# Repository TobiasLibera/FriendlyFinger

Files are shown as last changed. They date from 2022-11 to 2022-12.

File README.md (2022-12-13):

# FriendlyFinger

A lovely stress relief device I designed while having a week off from work.<br></br>

## Description ##

The FriendlyFinger is a machine which rotates a 3D model of a middle finger from one side to the other, while having two LEDs shining a little lightshow to it.\
It's based on an ESP32 Development Board and is designed for remote control via WebServer or UDP.\
You need a 3D printer for building this project as well as you need to be willing to put some effort into it.
For example you will need to solder a little curcuit.<br></br>
I had a lot of fun developing and building the Friendly Finger.\
I do hope you gain something from building it, too.<br></br>

A Video can be found here:\
[Youtube Video](https://youtu.be/8vTFOdNh7Bw)<br></br>
Thingiverse:\
[Printing Data](https://www.thingiverse.com/thing:5678932)<br></br>

## Printing ##

### Before you start the Printing ###

<p><strong>
  There is a "FF_Template_Fits" part, which has all fits in it, that are needed for the assembly.
  The dimensions of the holes are the ones, that I use to get good fits.
  I strongly recommend to print this part at least once to check if all fits are working properly before printing the actual parts.
</strong><br>
</p>

The fits in the ```FF_Template_Fits``` part are:

<ol>
  <li>Fit with Nema17 Stepper motor
    <ol>
      <li>Nominal:    22mm</li>
      <li>My Value:   22.4mm</li>
    </ol>
  </li>
  <li>Fit to screw in a M3 screw directly into the printing part
    <ol>
      <li>Nominal:    3mm</li>
      <li>My Value:   2.93mm</li>
    </ol>
  </li>
  <li>Fit for RGB LED with an 28° angle to the vertical axis
    <ol>
      <li>Nominal:    5mm</li>
      <li>My Value:   5mm</li>
    </ol>
  </li>    
  <li>Countersunk hole for M3 screw (standard: ISO 4762)</li>
</ol>

Feel free to modify the corresponding STEP files to make this fits work properly.

### Cura Settings ###

<p><strong>
  Change the "Overhang Angle" in the Cura Support settings to 46 degrees.
</strong><br>
</p>

There is a BOM for the printing parts in the Documentations directory where you can find the Cura settings I used, how long the print took and how much filament was needed.
As mentioned, that are my settings. I am very sure there are a lot of folks out there who can find better, more effective settings for their prints.<br></br>

## Electronics ##

### Curcuit Board ###

<p><strong>
  I don't own any degrees in electronics!
  So I won't make any further advises on how to design the curcuit itself.
  All I do is giving an example without any warranty for safety and functionality.
</strong><br>
</p>

There is a wiring diagram in the "Documentation" directory, where the basics of the curcuit are shown in the way I planned them for my own work. It's missing headers for the RGB-LEDs as it's missing headers for the Step-Down voltage regulator.
  
  As I like JST headers and Dupoint headers, I used them for my own version.
Feel free to use whatever floats your boat to realize this connections.

### Nema 17 Stepper Motor ###

The Nema 17 I used to design this device for, has a body length of ***38mm***. As there are a lot of alternative dimensions for Nema 17 stepper motors, you can definitly use smaller ones for your device. It's not much force needed to rotate the middle finger model. I can't recommend to use bigger ones, as I didn't test it... if you get a bigger one working, let me know.

### Stepper Motor Driver ###

The ***DRV8825*** is the driver I designed the code and the curcuit for. You can, of course, choose the driver you want to, but maybe need to adjust the code and the curcuit.\
***BUT:***
As far as I had the Friendly Finger run in my living room, I realised that dissipated heat is sure an issue of my design. To solve the problem I adjusted the current to ***75% - 80%*** of the nominal value of the stepper motor.\
Look for some help on the World Wide Web how to adjust the current with the stepper driver you use.\
In case of the ***DRV8825*** you need to regulate the value of voltage of the trimmer on the driver board to half of the value of current you want to have flow threw your motor. (And be careful with the trimmer, though)

### Fit with LM2596 DC-DC Step Down Module ###

There is a need to drill two holes into the breadboard to fit the LM2596 to it.
The ```FF_Washer_Distance``` part is for spacing between the breadboard and the LM2596.
The ```FF_Washer_ScrewIn``` part works as a nut for the M3x8 socket-head screws. It should be also possible to use standard M3 nuts (ISO 4032 | ISO 4033) for this.

### Connection with Base ###

There are screw holes in the ```FF_Base``` part which have a distance of ***71.12mm*** to each other. That's is the exact distance of 29 drillings in a breadboard with a ***2.54mm spacing***, which means, if you use this drillings and widen them to, maybe, 3.5mm, you can use them to connect the curcuit board to the ```FF_Base``` part with 4 screws.
It's designed to work with M3x8 socket head screws (ISO 4762).

### Fit into the Body ###

To fit a 100x100mm Breadboard into the base, there is the need of getting rid of the edges.
Therefor is the ```FF_Template_Edge``` part, which can be hold to each edge of the curcuit board. Then draw a line along the radius and grind away all the material thats behind that line.
That should be sufficient to fit the curcuit board into the ```FF_Body``` part.<br></br>

## Code ##

### Arduino IDE ###

For uploading the Code to the ESP32 Development Board I recommend the Arduino IDE.
You need to have the ESP32 support installed. Look on the World Wide Web for instructions how to do that. It's fairly simple.

### Dependencies ###

The Code has dependencies for some Standard Libraries of the Arduino IDE + ESP32 Standard Libraries.

There is one single additional dependcy. The ```analogWrite.h``` lib, which is designed for ESP32 and published under MIT licence.<br></br>
[Library description on www.arduino.cc](https://www.arduino.cc/reference/en/libraries/esp32-analogwrite/)<br></br>
You can install this library by using the Library Manager of the Arduino IDE.

### Adjustments to the Code ###

There is a pretty big ```#define``` section on top of the code, where you can do some settings.
Necessary is the IP address you want to use for the ESP32 as well as the password to your local network.

You can also define, if you want to control the FriendlyFinger by a webserver hosted on the ESP32. Or if you want the ESP32 as a UDP receiver for controlling. That's the setting I use, cause I control the Friendly Finger with a website in my local network which is hosted on a Raspberry Pi.

The other settings can be set as it's pleasing to you. Feel free to mess around a little.<br></br>

## Assembling the FriendlyFinger ##

*"It's a little bit tricky here and there..."*

### LEDs to Body ###

I won't lie to you. It's really pain in the a** to fit them in. I used WD40 as lube and still had problems to to this. Also you need to lead the cables down to the curcuit board while the stepper motor and the middle finger are already in the assembly.\
But it's possible, so I think you will get this done.

### Axis to Middle Finger ###

You need to glue the ```FF_Axis``` part to the ```FF_MiddleFinger``` part. I used fast drying epoxy glue which did the job quite well.<br></br>

## Credits ##

### Middle Finger ###

The original 3D model for the middle finger itself was desgined by ```Dmitrij Drandarov``` alias ```DahakaMVI```.
The file can be found on [Thingiverse](https://www.thingiverse.com/thing:4923022).

### GrabCAD ###

I used a lot of 3D models from [GrabCAD](https://grabcad.com).
I can absolutely recommend this website for 3D Models for standard parts, especially for electronic parts.

### ESP32 Webserver ###

As I didn't had much experience with webservers hosted on an ESP32, I used a tutorial as a base for my version of the code.
The tutorial I used was the [ESP32 Webserver Tutorial](https://lastminuteengineers.com/creating-esp32-web-server-arduino-ide/).<br></br>

## Donations ##

I want to dedicate this work to organizations which commit themselfs to helping people with mental illness.
Therefor I want to ask you to donate a little tip for one of the following organizations on www.betterplace.org, as long as you feel comfortable with that.\
I do not gain anything from it, and the organizations don't even know, I am sharing their links.
<br></br>
[Irrsinnig Menschlich e.V.](https://www.betterplace.org/de/organisations/2508-irrsinnig-menschlich-e-v)\
Translated Name: *Insanely Humane* (registered association)
<br></br>
[Stiftung Deutsche Depressionshilfe](https://www.betterplace.org/de/organisations/24384-stiftung-deutsche-depressionshilfe)\
Translated Name: *German Depression Help* (foundation)
<br></br>
***Thank you very much!***

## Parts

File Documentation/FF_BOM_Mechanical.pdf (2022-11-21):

BOM – Mechanical Parts | 2022-11-20 Tobias Libera
Name | Description | Standard | Amount | Link / Comment
Nema17 17HE15 | Stepper Motor | Nema 17 | 1 | https://www.amazon.de/gp/product/B0B38GX54H/
Coupler 5/8mm | 5mm to 8mm | | 1 | https://www.amazon.de/gp/product/B088R8CW5Z/
M3x8 Screw | Socket-Head Screw | ISO 4762 | 18
Feet Pads 8.5 x 2.5 | Self-adhesice rubber pads | | 4 | https://www.amazon.de/gp/product/B06XD47D79/

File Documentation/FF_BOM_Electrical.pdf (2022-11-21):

BOM – Electrical Parts | 2022-11-20 Tobias Libera
Name | Description | Standard | Value / Size | Amount | Link / Comment
Breadboard | Hard-paper | 2.54mm spacing | 100 x 100 mm | 1
ESP32 Development Board | ESP32 DevKitC – V4 | ESP32 | | 1
DRV8825 | Stepper Motor Driver | | | 1
LM2596 | DC-DC Step-Down | | 5V | 1
Input Jack | DC – Hollow Plug | | 5.5 x 2.1 mm | 1 | https://www.amazon.de/gp/product/B093FTFZ8Q
RGB-LED | Common-Cathode | | 2
Resistor | DIP | 470 Ohm | 6
Capacitor | DIP | 100 uF | 1
Header | Power Input | JST | 1x2 | 1 | For this items, there is always needed the header for the curcuit boards as well as the corresponding plug
Header | LM2596 | JST | 1x2 | 2
Header | RGB-LED | JST | 1x4 | 2
Header | Stepper Motor | Dupoint – Male | 1x4 | 1
Cables | Various Cables | Stranded
Isolation Sleeves | Various Sleeves

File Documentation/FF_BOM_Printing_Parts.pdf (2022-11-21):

BOM – Printing Parts | 2022-11-20 Tobias Libera
File Name | Amount | Material | Infill Density | Speed | Layer Thickness | Support | Adhesion | Material Weight | Time
FF_Body | 1 | PLA | 30 % | 85 mm/s | 0.2 mm | yes | no | 139 g | 14h 4m
FF_MotorPlate | 1 | PLA | 30 % | 60 mm/s | 0.2 mm | no | yes | 8 g | 59m
FF_Base | 1 | PLA | 30 % | 80 mm/s | 0.2 mm | yes | yes | 59 g | 5h 0m
FF_Axis | 1 | PLA | 100 % | 25 mm/s | 0.2 mm | no | yes | 2 g | 23m
FF_MiddleFinger | 1 | PLA | 30 % | 50 mm/s | 0.2 mm | yes | yes | 36 g | 5h 13m
FF_Washer_Distance | 2 2 | PLA PLA | 100 % | 60 mm/s 60 mm/s | 0.2 mm 0.2 mm | no no | no no | 1g | 4m FF_Washer_SrewIn
| | | 100 %
FF_Template_Edge | 1 | PLA | 100 % | 60 mm/s | 0.2 mm | no | no | 3 g | 22m
FF_Template_Fits | 1 | PLA | 30 % | 60 mm/s | 0.2 mm | no | no | 4 g | 36m

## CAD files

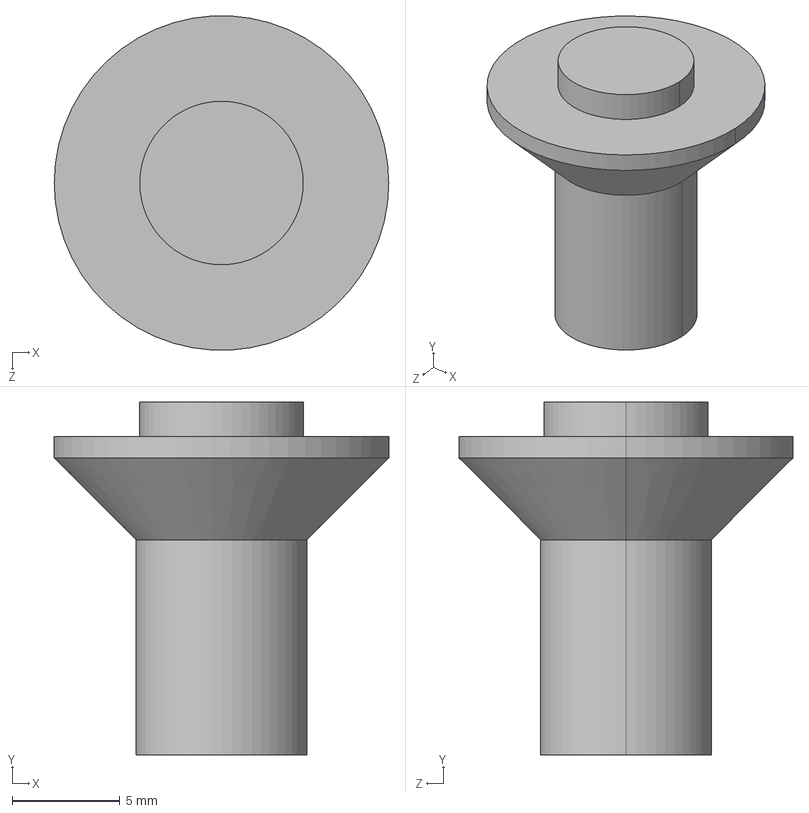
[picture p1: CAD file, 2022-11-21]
3D-Files/STEP/Printing_Parts/FF_Axis.STEP
15.5 x 16.4 x 15.5 mm

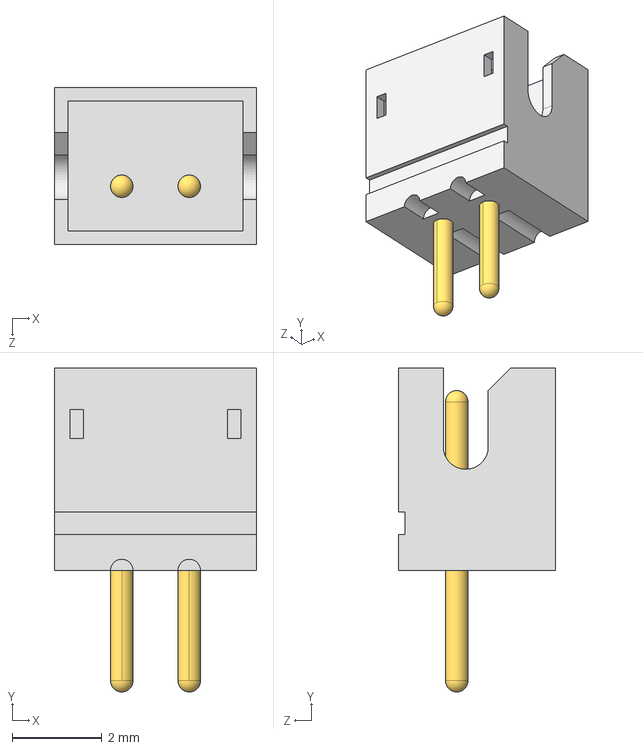
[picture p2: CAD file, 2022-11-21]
3D-Files/STEP/Purchase_Electrical/FF_PurchaseElectrical_HeaderMale_JST_1x2.STEP
4.50 x 7.20 x 3.50 mm

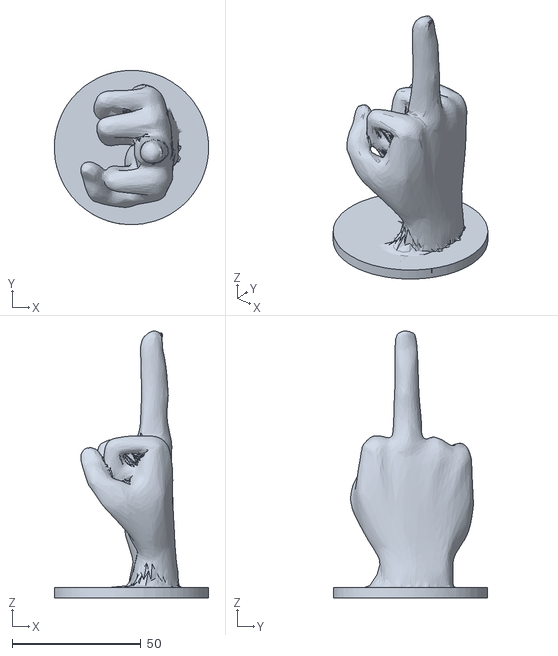
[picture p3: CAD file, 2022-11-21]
3D-Files/STL/FF_MiddleFinger.STL
60.0 x 60.0 x 103.8

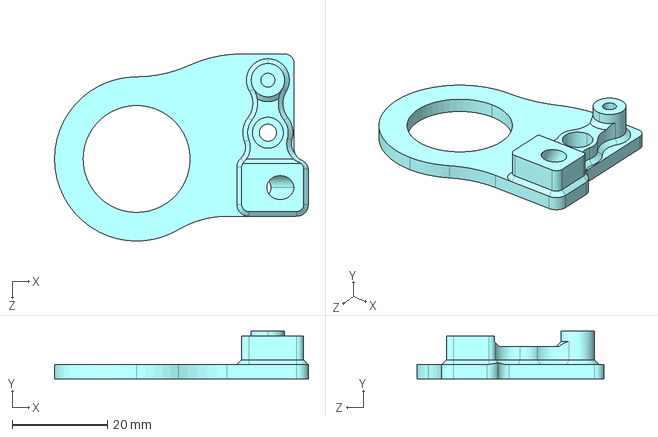
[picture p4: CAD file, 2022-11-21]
3D-Files/STEP/Printing_Parts/FF_Template_Fits.STEP
53.2 x 10.0 x 39.2 mm

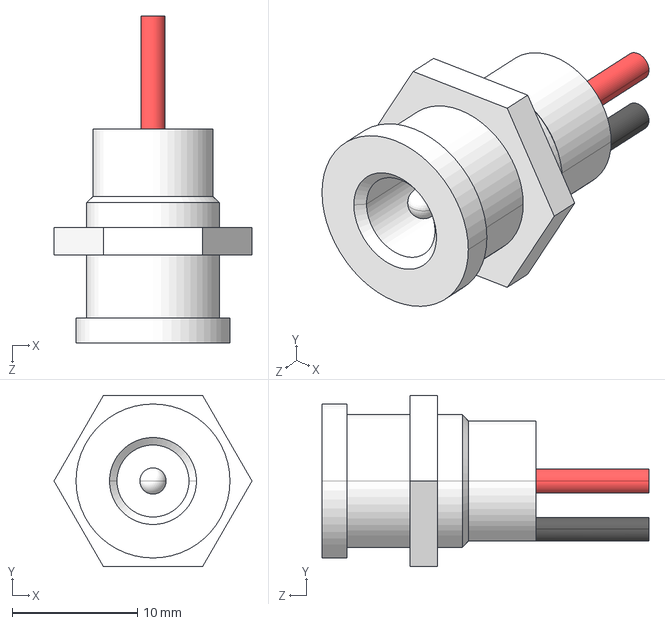
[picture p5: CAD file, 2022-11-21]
3D-Files/STEP/Purchase_Electrical/FF_PurchaseElectrical_Plug_5,5x2,1.STEP
15.8 x 13.7 x 26.1 mm

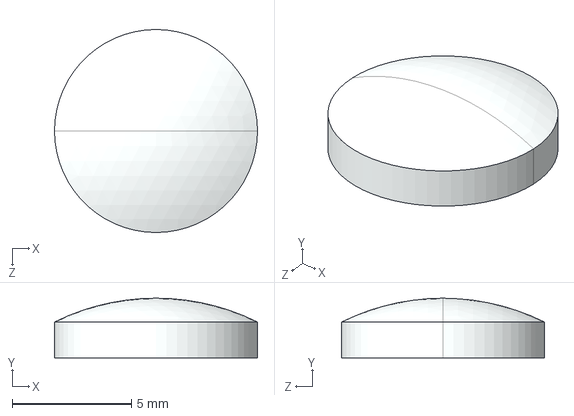
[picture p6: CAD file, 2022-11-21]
3D-Files/STEP/Purchase_Mechanical/FF_PurchaseMechanical_RubberFoot_8,5x2,5.STEP
8.50 x 2.50 x 8.50 mm

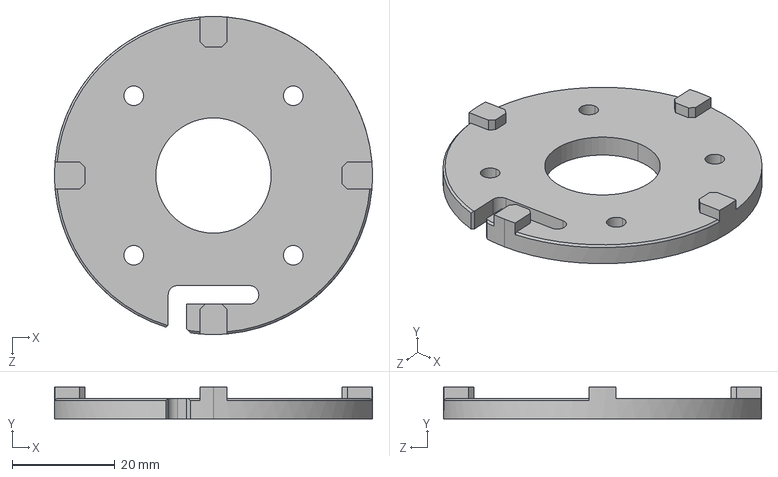
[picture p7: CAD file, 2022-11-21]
3D-Files/STEP/Printing_Parts/FF_MotorPlate.STEP
61.8 x 6.20 x 61.8 mm

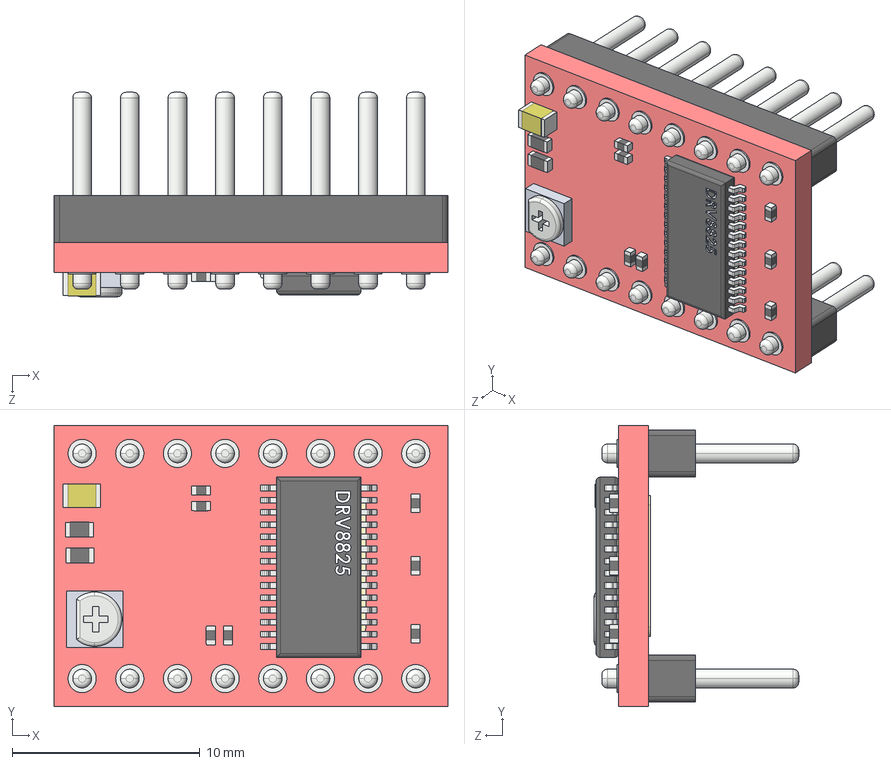
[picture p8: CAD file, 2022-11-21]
3D-Files/STEP/Purchase_Electrical/FF_PurchaseElectrical_DRV8255.STEP
21.0 x 15.0 x 10.9 mm
PCB
SMD Pot
0603 Resistor x 2
0805 Capacitor
0402 Resistor x 7
DRV8825 IC
8 pin Header x 2

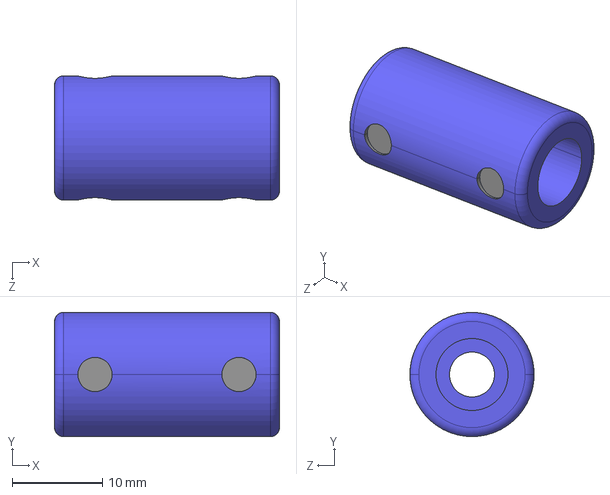
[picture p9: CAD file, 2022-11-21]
3D-Files/STEP/Purchase_Mechanical/FF_PurchaseMechanical_Cuppler_5-8.STEP
25.0 x 13.8 x 13.8 mm

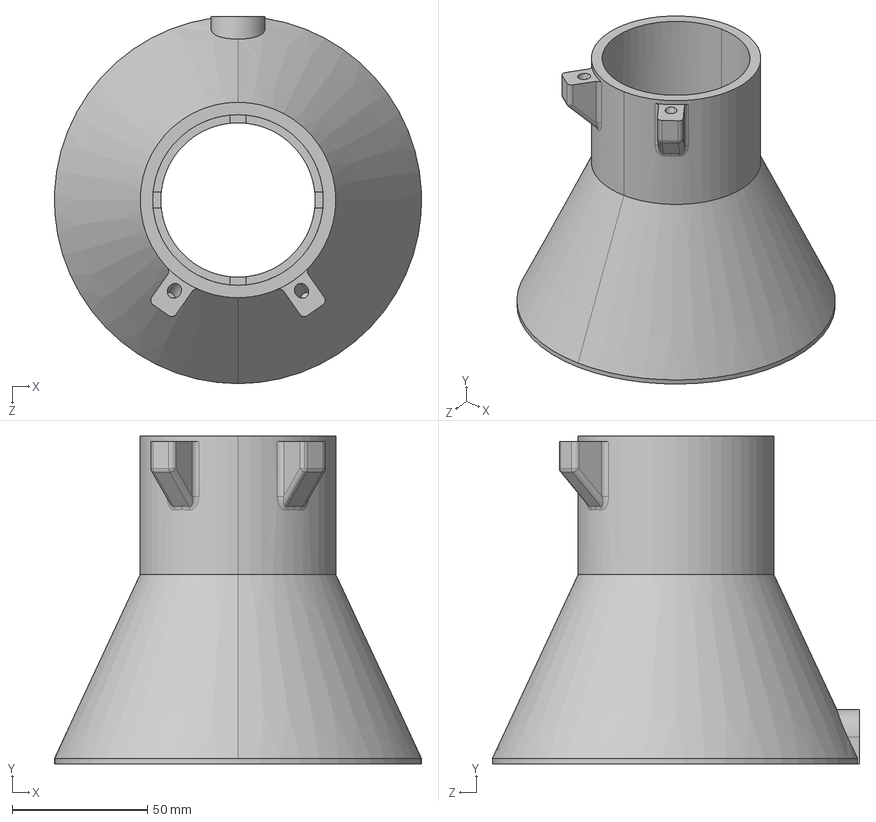
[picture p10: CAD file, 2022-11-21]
3D-Files/STEP/Printing_Parts/FF_Body.STEP
135.5 x 121.0 x 135.6 mm

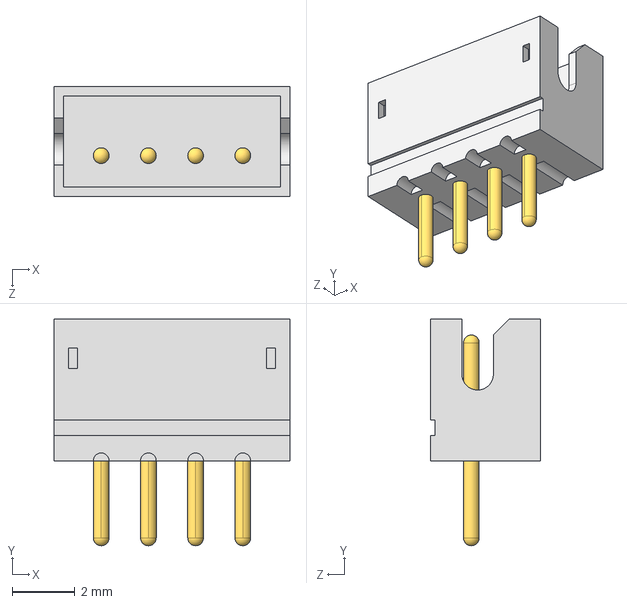
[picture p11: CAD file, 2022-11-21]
3D-Files/STEP/Purchase_Electrical/FF_PurchaseElectrical_HeaderMale_JST_1x4.STEP
7.50 x 7.20 x 3.50 mm

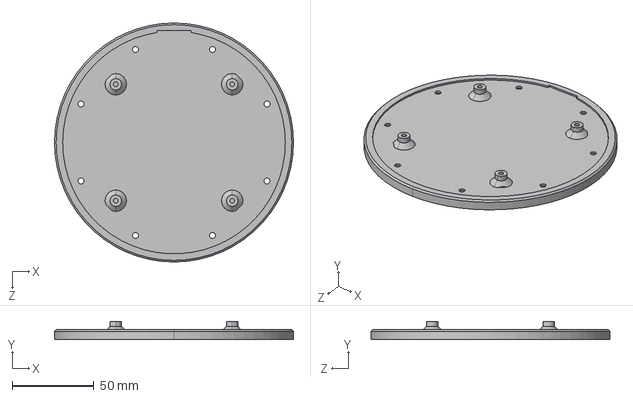
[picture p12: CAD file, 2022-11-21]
3D-Files/STEP/Printing_Parts/FF_Base.STEP
146.0 x 11.0 x 146.0 mm

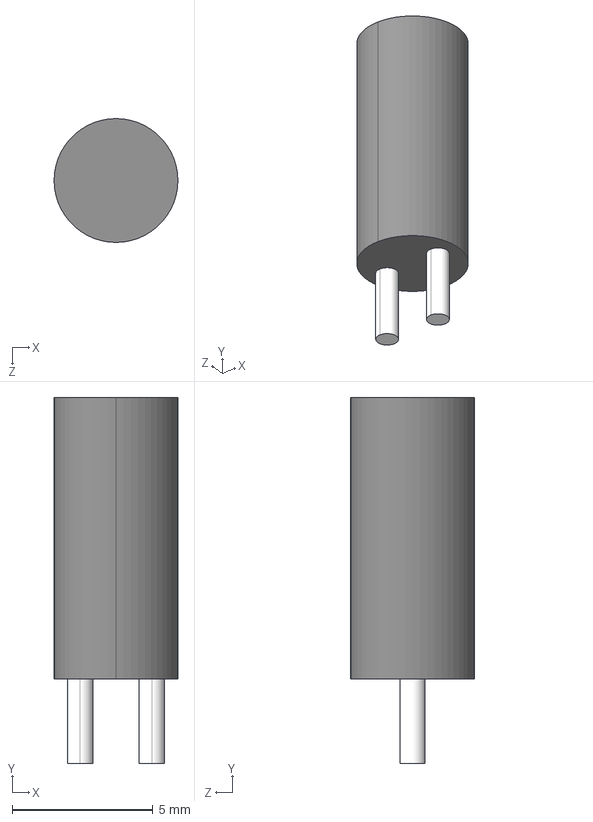
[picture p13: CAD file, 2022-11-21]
3D-Files/STEP/Purchase_Electrical/FF_PurchaseElectrical_Capacitor_100uF.STEP
4.40 x 13.0 x 4.40 mm

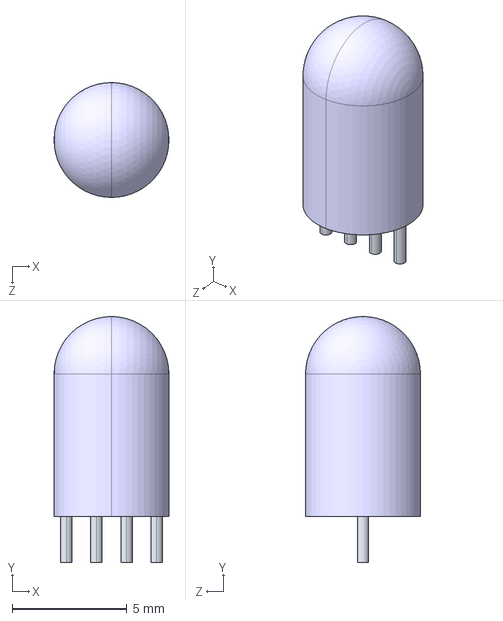
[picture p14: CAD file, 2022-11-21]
3D-Files/STEP/Purchase_Electrical/FF_PurchaseElectrical_RGB-LED_CommonCathode_5mm.STEP
5.00 x 10.7 x 5.00 mm

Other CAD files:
3D-Files/STEP/Printing_Parts/FF_Template_Edge.STEP
3D-Files/STEP/Purchase_Electrical/FF_PurchaseElectrical_Resistor_470.STEP
3D-Files/STEP/Purchase_Electrical/FF_PurchaseElectrical_HeaderMale_Dupoint_1x4.STEP
3D-Files/STEP/Purchase_Mechanical/FF_PurchaseMechanical_SocketHeadScrew_ISO4762_M3x8.STEP
3D-Files/STEP/Printing_Parts/FF_Washer_Distance.STEP
3D-Files/STEP/Printing_Parts/FF_Washer_ScrewIn.STEP
3D-Files/STL/FF_Axis.STL
3D-Files/STL/FF_Base.STL
3D-Files/STL/FF_Body.STL
3D-Files/STL/FF_MotorPlate.STL
3D-Files/STL/FF_Template_Edge.STL
3D-Files/STL/FF_Template_Fits.STL
3D-Files/STL/FF_Washer_Distance.STL
3D-Files/STL/FF_Washer_ScrewIn.STL

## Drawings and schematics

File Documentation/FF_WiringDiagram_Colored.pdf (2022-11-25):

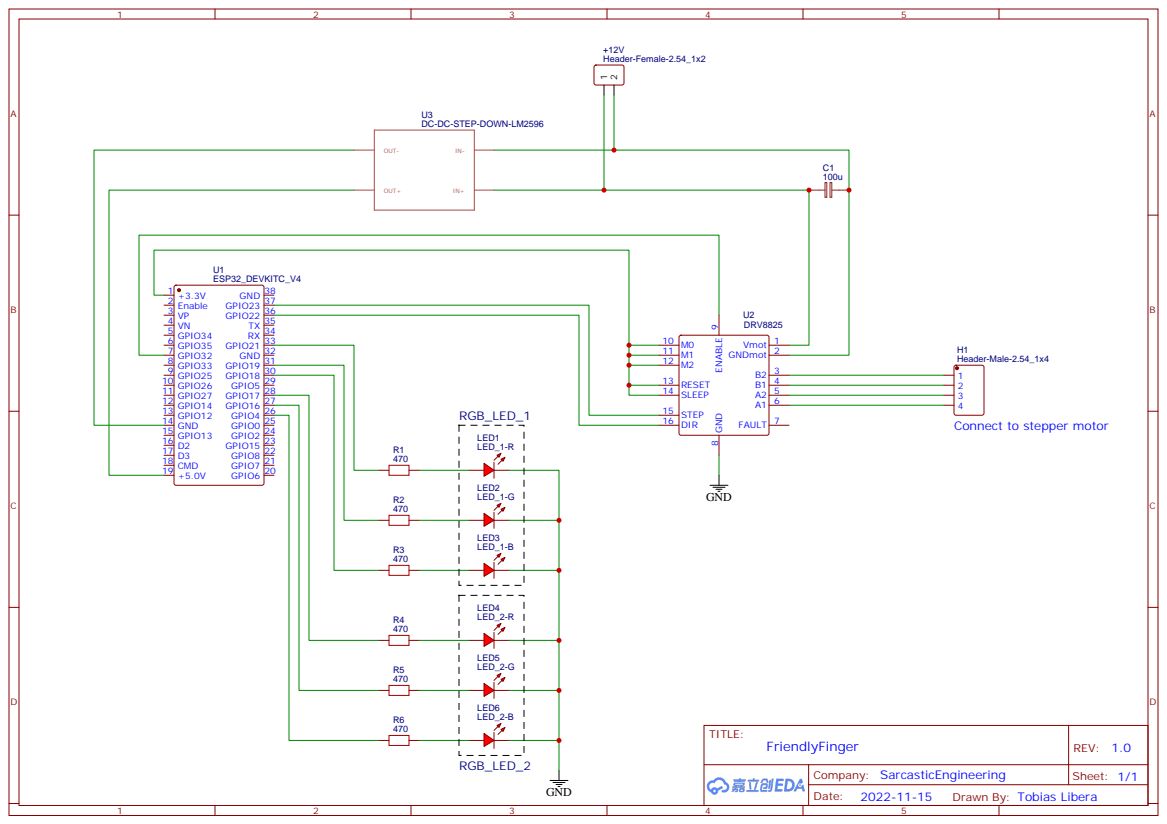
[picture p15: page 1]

DC-DC-STEP-DOWN-LM2596

Drawn By: Tobias Libera

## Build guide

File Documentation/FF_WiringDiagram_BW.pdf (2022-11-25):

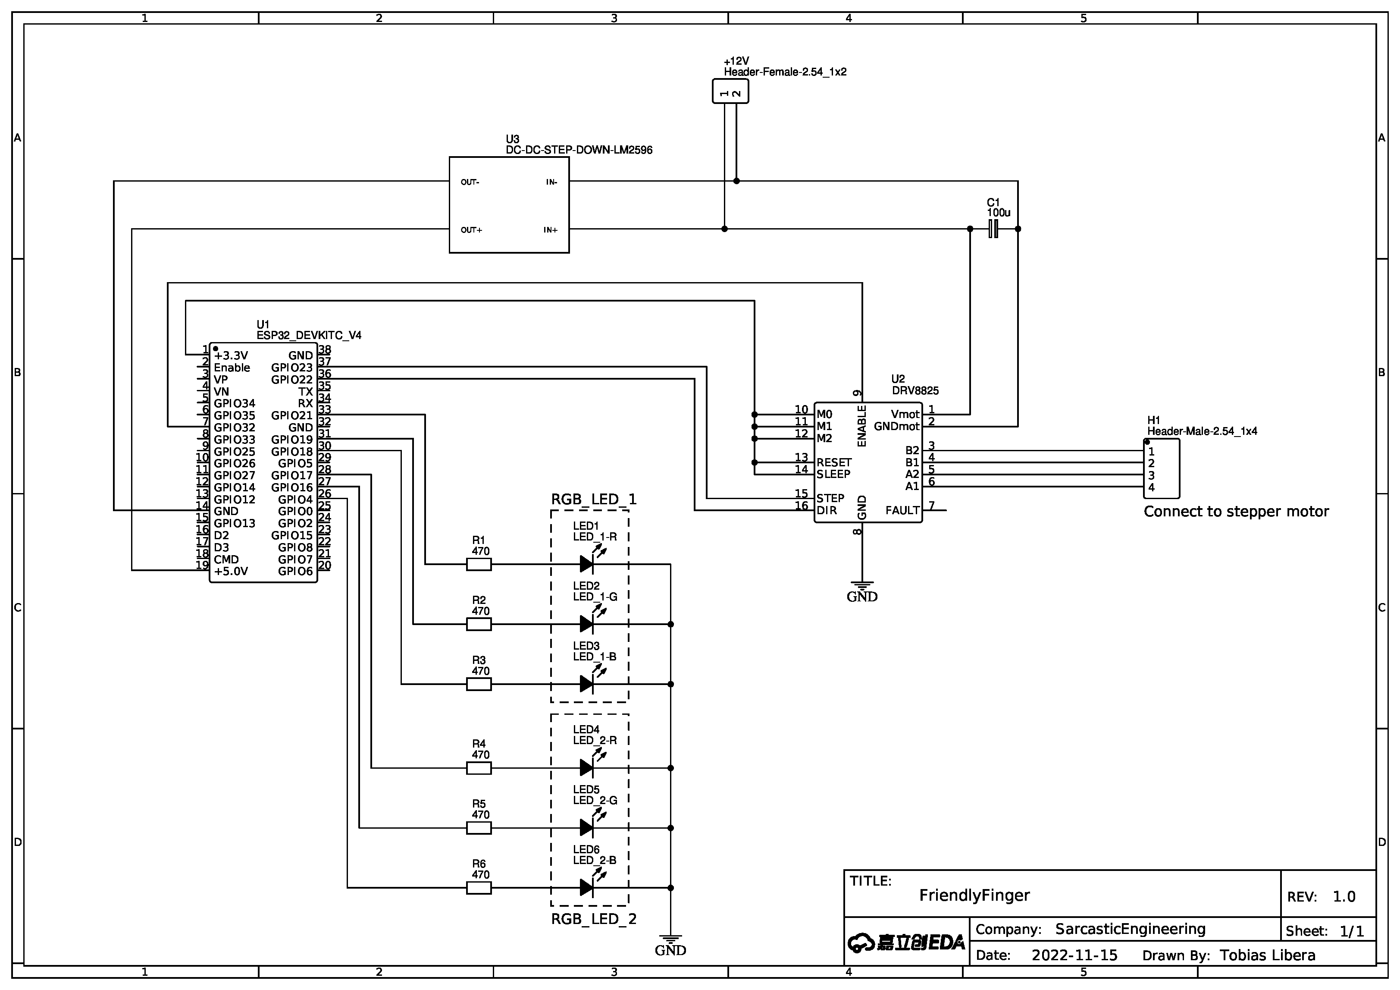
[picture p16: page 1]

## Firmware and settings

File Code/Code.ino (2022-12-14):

/*
 * Code for the FriendlyFinger project.
 * Written by Tobias Libera and published under the alias "SarcasticEngineering".
 * 
 * All data for this project can be found here:
 * https://github.com/TobiasLibera/FriendlyFinger
 * 
 * All data of this project is licensed under the
 * GNU General Public License 3
 * 
 * 2022-12-03
 */
 
#include <WiFi.h>
#include <Arduino.h>

#include <analogWrite.h>



/*
 * Pin Definitions
 */

#define STEPPER_STP         23
#define STEPPER_DIR         22
#define STEPPER_EN          32

#define RGB_L_RED           21
#define RGB_L_GRN           19
#define RGB_L_BLU           18

#define RGB_R_RED           17
#define RGB_R_GRN           16
#define RGB_R_BLU           4



/*
 * WiFi Definitions
 */

IPAddress LOCAL_IP          (192, 168, 1,   2) ;
IPAddress GATEWAY           (192, 168, 1,   1) ;
IPAddress SUBNET            (255, 255, 255, 0) ;
IPAddress DNS               (192, 168, 1,   1) ;

#define WIFI_NAME           "your_funny_wifi_name"
#define WIFI_PASSWORD       "your_secure_wifi_password_123456"

#define WIFI_RECONNECT_TIMEOUT  5000                            /* Milliseconds of not available Wifi, until reconnect try */



/*
 * Controls Definitions
 */
                                              /* ATTENTION: Only have one of the Control Definitions uncommented! */
#define WEBSERVER                             /* If defined: The ESP32 will host a webserver for turning the Friendly Finger on and off *//
//#define UDP_SERVER                          /* If defined: Enables the receiving of UDP messages for turning the Friendly Finger on and off */

#define _SERVER_PORT                    80    /* Port where Webserver will be hosted OR UDP-server is listening */

#define WEBSERVER_BACKGROUND_COLOR      String("#A9A9A9")   /* Color definitions for the webserver */
#define WEBSERVER_TITLE_COLOR           String("#000000")
#define WEBSERVER_BUTTON_ON_COLOR       String("#008B8B")       
#define WEBSERVER_BUTTON_OFF_COLOR      String("#556B2F")
#define WEBSERVER_BUTTON_TEXT_COLOR     String("#FFFFFF")

#define UDP_FF_ON                       42    /* Message to receive to enable the functions of the Friendly Finger */
#define UDP_FF_OFF                      69    /* Message to receive to disable the functions of the Friendly Finger */



/*
 * Movement Definitions
 */

#define MOVEMENT_ANGLE                130       /* Movement angle from complete to the left to complete to the right */
#define MOVEMENT_SPEED                8         /* Duration in seconds for one movement from left to right */
#define STEPS_PER_ROTATION            6400      /* Number of steps for one rotation of the stepper motor (Microstepping) */
#define TIME_AT_DIRECTION_REVERSE     300       /* Number of milliseconds to wait at movment extreme point before direction is reversed */



/*
 *  Lightshow Definitions
 */

#define BLINK_DOUBLE_ON               300       /* Duration in milliseconds the light stays on */
#define BLINK_DOUBLE_OFF              750       /* Duration in milliseconds the light stays off */
#define BLINK_DOUBLE_CYCLES           4         /* Number of cycles the blink double programm is running through */

#define RAINBOW_CYCLE_TIME            20        /* Duration in seconds from starting a color till the color is reached again */
#define RAINBOW_CYCLES                2         /* Number of cycles the rainbow programm is running through */
 
#define BLINK_SINGLE_ON               300       /* Duration in milliseconds the light stays on */
#define BLINK_SINGLE_OFF              300       /* Duration in milliseconds the light stays off */
#define BLINK_SINGLE_CYCLES           5         /* Number of cycles the blink double programm is running through */

#define RAINBOW_SPLITTED_SWITCH_TIME  250       /* Time afted LED is switched */
#define RAINBOW_SPLITTED_CYCLE_TIME   13        /* Duration in seconds from starting a color till the color is reached again */
#define RAINBOW_SPLITTED_CYCLES       4         /* Number of cycles the rainbow programm is running through */

#define WHITE_BLINK_TIMEOUT_BEGIN     500       /* On-Off time in milliseconds where white blink starts */
#define WHITE_BLINK_TIMEOUT_DECRMNT   30        /* On-Off time decrement in milliseconds per blink */
#define WHITE_BLINK_TIMEOUT_FADE      4         /* Fade timeout in milliseconds for each change in brightness */

#define LIGHTSHOW_ALL_OVER_CYCLES     3         /* Number of cycles to walk through blink and rainbow program till while blink cycle end */




#ifdef WEBSERVER
  #include <WebServer.h>
  WebServer server ( _SERVER_PORT ) ;
#endif

#ifdef UDP_SERVER
  #include <WiFiUdp.h>
  WiFiUDP server ;
#endif




bool DO_FUNCTIONS = false ;




#ifdef WEBSERVER
  class WebServerManager
  {
  
    public:
  
      WebServerManager (WebServer* server)
      {
        /* 
         * Constructor for Class WebServerManager 
         * Takes a pointer to Webserver Class as argument
         */
        this -> web_server = server ;
      }
    
    
      void init(uint16_t dummy_port)
      {
        /*
         * Defines the subdomains
         * Inits the webserver
         */
        this -> web_server -> on("/"      , this->handle_connect) ;
        this -> web_server -> on("/ff_on" , this->handle_ff_on) ;
        this -> web_server -> on("/ff_off", this->handle_ff_off) ;
        
        this -> web_server -> onNotFound(this->handle_not_found) ;
    
        this -> web_server -> begin() ;
      }
    
    
      void work()
      {
        /*
         * This function will be called from main loop() function
         * Handles client requests to the webserver
         */
        this -> web_server -> handleClient() ;
      }
  
  
    private:
  
      static void handle_connect()
      {
        /*
         * Handles subdomain "/"
         */
        server.send(200, "text/html", send_HTML(DO_FUNCTIONS)) ; 
      }
    
    
      static void handle_ff_on()
      {
        /*
         * Handles subdomain "/ff_on"
         * Enables the functions of the Friendly Finger
         */
        DO_FUNCTIONS = true ;
        server.send(200, "text/html", send_HTML(DO_FUNCTIONS)) ; 
      }
    
    
      static void handle_ff_off()
      {
        /*
         * Handles subdomain "/ff_off"
         * Disables the functions of the Friendly Finger
         */
        DO_FUNCTIONS = false ;
        server.send(200, "text/html", send_HTML(DO_FUNCTIONS)) ; 
      }
    
    
      static void handle_not_found()
      {
        /*
         * Handling of all subdomains, which are not defined
         */
        server.send(404, "text/plain", "Not found") ;
      }
    
    
      static String send_HTML (bool is_functions)
      {
        /*
         * HTML script, which is send to the client
         */
        String ptr = "<!DOCTYPE html> <html>\n" ;
          ptr +="<head><meta name=\"viewport\" content=\"width=device-width, initial-scale=1.0, user-scalable=no\">\n" ;
          ptr +="<title>Friendly Finger Control</title>\n" ;
          ptr +="<style>html { font-family: Helvetica; display: inline-block; margin: 0px auto; text-align: center;}\n" ;
          ptr +="body{margin-top: 50px;background-color:"+WEBSERVER_BACKGROUND_COLOR+"} h1 {color: "+WEBSERVER_TITLE_COLOR+";margin: 50px auto 30px;}\n" ;
          ptr +=".button {display: block;width: 80px;;border: none;color: "+WEBSERVER_BUTTON_TEXT_COLOR+";padding: 13px 30px;text-decoration: none;font-size: 25px;margin: 0px auto 35px;cursor: pointer;border-radius: 4px;}\n" ;
          ptr +=".button-on {background-color: "+WEBSERVER_BUTTON_ON_COLOR+";}\n" ;
          ptr +=".button-off {background-color: "+WEBSERVER_BUTTON_OFF_COLOR+";}\n" ;
          ptr +="p {font-size: 14px;color: #888;margin-bottom: 10px;}\n" ;
          ptr +="</style>\n" ;
          ptr +="</head>\n" ;
          ptr +="<body>\n" ;
          ptr +="<h1>Friendly Finger</h1>\n" ;
          
          if (is_functions)
          {ptr +="<a class=\"button button-off\" href=\"/ff_off\">OFF</a>\n" ;}
          else
          {ptr +="<a class=\"button button-on\" href=\"/ff_on\">ON</a>\n" ;}
    
          ptr +="</body>\n" ;
          ptr +="</html>\n" ;
          return ptr ;
      }
    
    
      WebServer* web_server ;
    
  } ;
#endif




#ifdef UDP_SERVER
  class UdpServerManager
  {
    
    public:
  
      UdpServerManager (WiFiUDP* server)
      {
        /* 
         * Constructor for Class UdpServerManager 
         * Takes a pointer to WiFiUDP Class as argument
         */
        this -> udp_server = server ;
      }


      void init(uint16_t port)
      {
        /*
         * Inits the UDP Server
         * Takes the port, on which the udp server is listening, as argument
         */
        this -> udp_server -> begin(port) ;
      }


      void work()
      {
        /*
         * This function will be called from main loop() function
         * Handles incoming UDP messages, checks if they correspond to the defined
         * Commands of enabling and disabling the functions of the Friendly Finger
         */
        int32_t packetSize = this -> udp_server -> parsePacket() ;
        if (packetSize)
        {
          for (uint8_t i = 0; i < 255; i += 1)
          {
            this -> packet[i] = 0 ;
          }
          
          this -> udp_server -> read(this->packet, 255) ;
          this -> udp_server -> flush() ;

          int16_t udp_input = atoi(this->packet) ;

          if (udp_input > 0)
          {
            if (udp_input == UDP_FF_ON)
            {
              DO_FUNCTIONS = true ;
            }
            else if (udp_input == UDP_FF_OFF)
            {
              DO_FUNCTIONS = false ;
            }
          }
        }
      }


    private:

      char packet[255] ;

      WiFiUDP* udp_server ;
      
  } ;
#endif




class WifiManager
{

  public:

    void init()
    {
      /*
       * Configuration of the WiFi settings of the ESP32 
       * Mainly sets the IP, which the ESP32 can be accessed at
       */
       WiFi.config(LOCAL_IP, GATEWAY, SUBNET, DNS) ;
    }

    void check()
    {
      /*
         * This function will be called from main loop() function
         * Handles the connection to the local network
         * Trys to reconnect to the local network if connection is broken
         */
      if (WiFi.status() != WL_CONNECTED)
      {
        if (millis() >= this->reconnect_timer + WIFI_RECONNECT_TIMEOUT)
        {
          WiFi.disconnect() ;
          WiFi.begin(WIFI_NAME, WIFI_PASSWORD) ;
          this->reconnect_timer = millis() ;
        }
        
        else if (this->reconnect_timer == 0)
        {
          WiFi.begin(WIFI_NAME, WIFI_PASSWORD) ;
          this->reconnect_timer = millis() ;
        }    
      }
    }


  private:

    uint64_t reconnect_timer = 0 ;
    
} ;




class Stepper
{

  public:

    Stepper (uint8_t stp_pin, uint8_t dir_pin, uint8_t en_pin)
    {
      /*
       * Constructor for Class for Stepper Motor
       * Defines Step Pin, Direction Pin and Enable Pin of the DRV8825 Stepper Motor Driver
       * Defines this pins as output and makes sure, the voltage level of the pins
       * are indeed set to 0V or 1V (Enable)
       * Calculates Parameters needed for the movement from global definitions
       * Sets current position to center position as thats where the movement starts
       */
      this -> stp_pin = stp_pin ;
      this -> dir_pin = dir_pin ;
      this -> en_pin  = en_pin ;

      pinMode(this->stp_pin, OUTPUT) ;
      pinMode(this->dir_pin, OUTPUT) ;
      pinMode(this->en_pin, OUTPUT) ;

      digitalWrite(this->stp_pin, 0) ;
      digitalWrite(this->dir_pin, 0) ;
      digitalWrite(this->en_pin, 1) ;

      this -> calc_parameters() ;

      this -> current_steps = this -> steps_per_half_move ;
    }


    void work()
    {
      /*
       * This function will be called from main loop() function and works with timers
       * Manages the movemet of the stepper motor
       */
      if (DO_FUNCTIONS || do_final_move)
      {
        /*
         * If functions of the Friendly Finger are enabled OR functions were shut off and Finger is moving to center position
         */
        digitalWrite(this->en_pin, 0) ;
         
        if (DO_FUNCTIONS && do_final_move)
        {
          /*
           * If functions of Friendly Finger are enabled while it's also moved to center position for shut down,
           * the mode for the final move is disabled
           */
          do_final_move = false ;
        }

        if (this->wait_for_reverse)
        {
          /*
           * If waiting for reverse direction, do nothing but waiting till timer is done
           */
          if (millis() >= this->wait_reverse_time + TIME_AT_DIRECTION_REVERSE)
          {
            this -> wait_for_reverse = false ;
          }
        }
        else
        {
          /*
           * If not waiting for reverse, wait for step timer and do one single step
           */
          if (millis() > this->last_step_time + this->millis_per_step)
          {
            this -> do_step() ;
            this -> last_step_time = millis() ;
          }
        }

        if (this->current_steps >= steps_per_full_move)
        {
          /*
           * Reverse direction, zero, steps and init the waiting for reverse  
           */
          this -> set_dir(!this->current_dir) ;
          this -> zero_steps() ;

          this -> wait_for_reverse = true ;
          this -> wait_reverse_time = millis() ;
        }
      }
      
      if (!DO_FUNCTIONS)
      {
        /*
         * If functions of the Friendly Finger is shut down
         */
        if (this-> current_steps != steps_per_half_move)
        {
          /*
           * Enables the movement to center position if current position is not center position
           */
          this -> do_final_move = true ;
        }
        else
        {
          /*
           * If current position is center position
           */
          if (this->do_final_move)
          {
            /*
             * Disables movement to center position and sets current direction to initial value
             */
            this -> do_final_move = false ;
          }
          this -> set_dir(0) ;
          digitalWrite(this->en_pin, 1) ;
        }
      }
    }


  private:

    void do_step()
    {
      /*
       * Does one single step
       */
      digitalWrite(this->stp_pin, 1) ;
      digitalWrite(this->stp_pin, 0) ;
      this -> current_steps += 1 ;
    }


    void zero_steps()
    {
      /*
       * Sets the current steps to zero
       */
      this -> current_steps = 0 ;
    }


    void set_dir(bool dir)
    {
      /*
       * Sets direction of stepper motor
       */
      digitalWrite(this->dir_pin, dir) ;
      this -> current_dir = dir ;
    }


    void calc_parameters()
    {
      /*
       * Calculates parameters for the movemet from global parameter definitions
       */
      this -> steps_per_full_move = (uint32_t)( (float)STEPS_PER_ROTATION * ( (float)MOVEMENT_ANGLE / 360.0 ) ) ;

      this -> steps_per_half_move = this->steps_per_full_move / 2 ;
      
      this -> millis_per_step = (uint64_t)( (MOVEMENT_SPEED * 1000) / this->steps_per_full_move ) ;
    }

    uint8_t   stp_pin ;
    uint8_t   dir_pin ;
    uint8_t   en_pin ;
    
    uint32_t  current_steps = 0 ;
    bool      current_dir   = 0 ;

    uint64_t  millis_per_step ;
    uint64_t  last_step_time = 0 ;
    
    uint32_t  steps_per_full_move ;
    uint32_t  steps_per_half_move ;

    bool      wait_for_reverse  = false ;
    uint64_t  wait_reverse_time = 0 ;

    bool      do_final_move = false ;

} ;




class RgbLed
{

  public:

    RgbLed (uint8_t red, uint8_t green, uint8_t blue)
    {
      /*
       * Constructor for Class for RGB-LED
       * Defines Pins for the red, green and blue anode of the RGB-LED
       * Defines this pins as output and makes sure, the voltage level of the pins
       * are indeed set to 0V
       */
      this -> r = red ;
      this -> g = green ;
      this -> b = blue ;

      pinMode(this->r, OUTPUT) ;
      pinMode(this->g, OUTPUT) ;
      pinMode(this->b, OUTPUT) ;

      digitalWrite(this->r, 0) ;
      digitalWrite(this->g, 0) ;
      digitalWrite(this->b, 0) ;
    }


    void write( uint8_t r_pwm, uint8_t g_pwm, uint8_t b_pwm)
    {
      /*
       * Function for writing PWM values to the 3 anodes of the RGB-LED.
       * Takes values from 0 - 255 which maps to 0 - 3.3V
       */
      analogWrite(this->r, r_pwm) ;
      analogWrite(this->g, g_pwm) ;
      analogWrite(this->b, b_pwm) ;
    }


    void off()
    {
      /*
       * Turns off the RGB-LED
       */
      analogWrite(this->r, 0) ;
      analogWrite(this->g, 0) ;
      analogWrite(this->b, 0) ;
    }


  private:

    uint8_t r ;
    uint8_t g ;
    uint8_t b ;

} ;
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
void loop()
{
  wifi_management.check() ;
  
  input_control.work() ;
  
  finger.work() ;
  lightshow.work() ;
}

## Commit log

2022-11-21 Added donation links and added assembly description
2022-11-21 Updated Mechanical BOM
2022-12-13 Renamed for better Arduino IDE Implementation
